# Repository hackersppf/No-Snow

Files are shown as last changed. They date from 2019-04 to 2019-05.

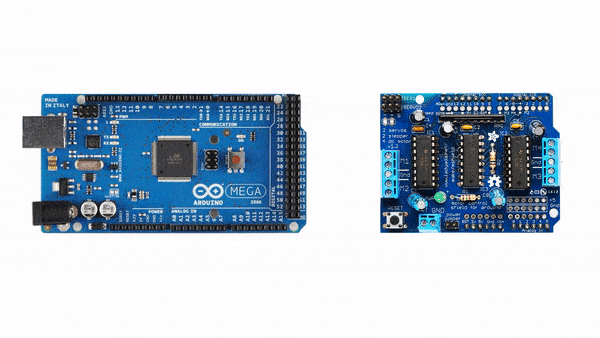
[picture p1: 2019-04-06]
Schematics/Motor Driver Shield connect to Mega.gif

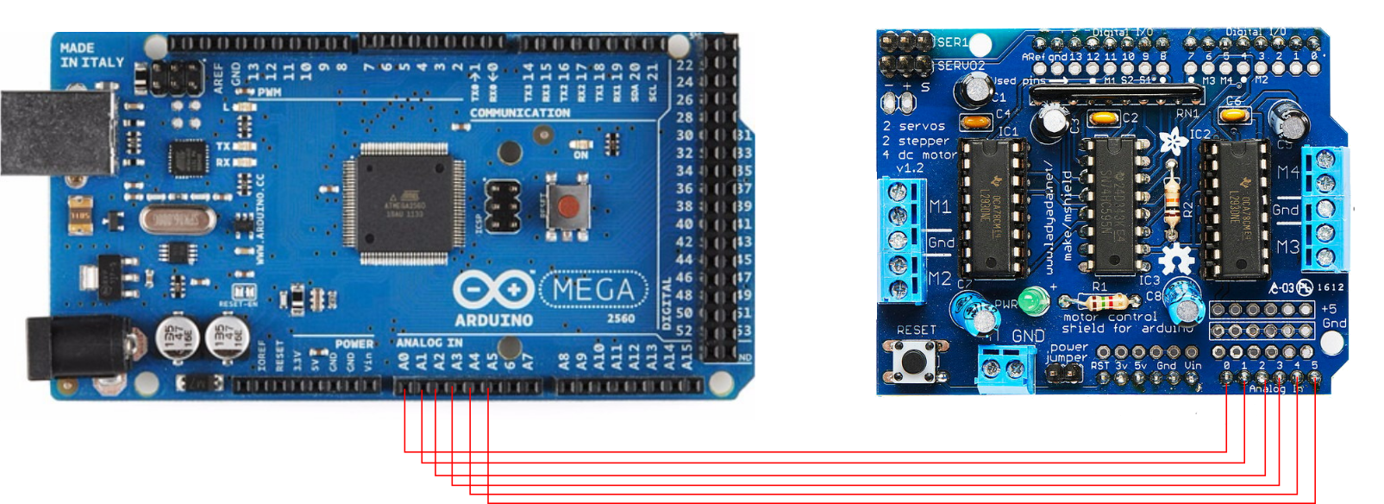
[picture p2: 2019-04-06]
Schematics/Motor Driver Shield connect to Mega.png

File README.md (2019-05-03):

# No-Snow
Ένα αυτόνομο αποχιονιστικό όχημα για τον καθαρισμό των αυλών στα σχολεία της Φλώρινας.
![](https://lh3.googleusercontent.com/xO7sTSYgVaHP3CewTKH7Cif9RfCc6hG_EpvHSLslNRIoFkOp1THHu7uWFASRAP4SzOY6zCx56El4OVzGu1Sz-iZWRYOYOWNuBQ8KCTcxCPi_N1hTWm2V-zk4BNUXDjUctix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)
Στην πόλη μας (Φλώρινα) κατά τους χειμερινούς μήνες έχουμε συχνά χιονοπτώσεις οι οποίες συνοδεύονται από χαμηλές θερμοκρασίες, με αποτέλεσμα προβλήματα στις μετακινήσεις, καθώς και στην λειτουργία των σχολείων. Ύστερα από κάθε ισχυρή χιονόπτωση, τα εκχιονιστικά μηχανήματα του Δήμου δουλεύουν συνεχώς για να καθαρίσουν τους δρόμους της πόλης και των γύρω χωριών, καθώς και τις αυλές των σχολείων πριν προλάβει να παγώσει το χιόνι. Αρκετές φορές τα σχολεία παραμένουν κλειστά γιατί δεν έχουν προλάβει να καθαριστεί οι αυλές, καθώς δίνεται προτεραιότητα τους δρόμους.

Επιλέξαμε λοιπόν να κατασκευάσουμε ένα αυτόνομο αποχιονιστικό μηχάνημα, το οποίο θα αναλαμβάνει να καθαρίσει το χιόνι από έναν συγκεκριμένο χώρο (για παράδειγμα την αυλή ενός σχολείου) χωρίς να χρειάζεται οδηγό.

#### Οι βασικές λειτουργίες που έχει το σύστημα μας είναι οι εξής:
- Μπορεί να κινηθεί σε ευθεία διαδρομή καθαρίζονας το χιόνι με το μαχαίρι και αντιλαμβάνεται τυχόν αποκλίσεις τις οποίες διορθώνει, με την βοήθεια γυροσκόπιου.
- Αντιλαμβάνεται πότε φτάνει στα όρια της αυλής με τον αισθητήρα απόστασης υπέρηχων και μπορεί να συνεχίσει την πορεία του προς την αντίθετη πλευρά με ακρίβεια αξιοποιώντας το γυροσκόπιο.
- Αντιλαμβάνεται την κίνηση ανθρώπων στον χώρο της αυλής (αισθητήρας PIR) και σταματάει εκπέμποντας προειδοποιητικά μηνύματα και φώτα.
- Αντιλαμβάνεται αν υπάρχουν συνθήκες δημιουργίας πάγου (αισθητήρας θερμοκρασίας και βροχόπτωσης) και να ρίχνει αλάτι στην αυλή.
#### Μελλοντικά σχέδια
- Υπολογισμός της θέσης του μέσα στην αυλή του σχολείου αξιοποιώντας τα δεδομένα από το γυροσκόπιο και τον αισθητήρα απόστασης.
- Επικοινωνία με έξυπνα κινητά τηλέφωνα ώστε να στέλνει και να δέχεται δεδομένα για την κατάσταση αποχιονισμού.

**Μπορείτε να διαβάσετε αναλυτικά για την υλοποίηση του έργου [στην ιστοσελίδα του ομίλου μας.](http://ppf.edu.gr/hackers/archives/604 "στην ιστοσελίδα του ομίλου μας.")**

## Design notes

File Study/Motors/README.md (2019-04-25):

Σε αυτό το εργαστήριο μελετήσαμε την αρχή λειτουργίας των κινητήρων DC, Servo και Stepper και τους τρόπους με τους οποίους μπορούμε να τους ελέγξουμε με την χρήση του Arduino. Στο πλαίσιο του εργαστηρίου κατασκευάσαμε και μερικούς ανεμιστήρες με φίλτρο, αξιοποιώντας παλιές συσκευές που υπάρχουν στο υπόγειο του σχολείου, τους οποίους χρησιμοποιήσαμε αργότερα για την απομάκρυνση των οσμών από την κόλληση καλωδίων. Μπορείτε να δείτε περισσότερες λεπτομέρειες στην ανάρτηση που υπάρχει εδώ: http://ppf.edu.gr/hackers/archives/604

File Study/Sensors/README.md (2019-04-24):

Εργαστήριο στο οποίο μελετάμε τον τρόπο με τον οποίο μπορούμε να λαμβάνουμε τιμές από τον φυσικό κόσμο και να τις μετατρέπουμε σε ψηφιακές τιμές με την χρήση αισθητήρων και του Arduino. Περισσότερες λεπτομέρειες στο http://ppf.edu.gr/hackers/archives/55

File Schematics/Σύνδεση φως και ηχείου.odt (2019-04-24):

## Σύνδεση μονάδων φωτός και ήχου

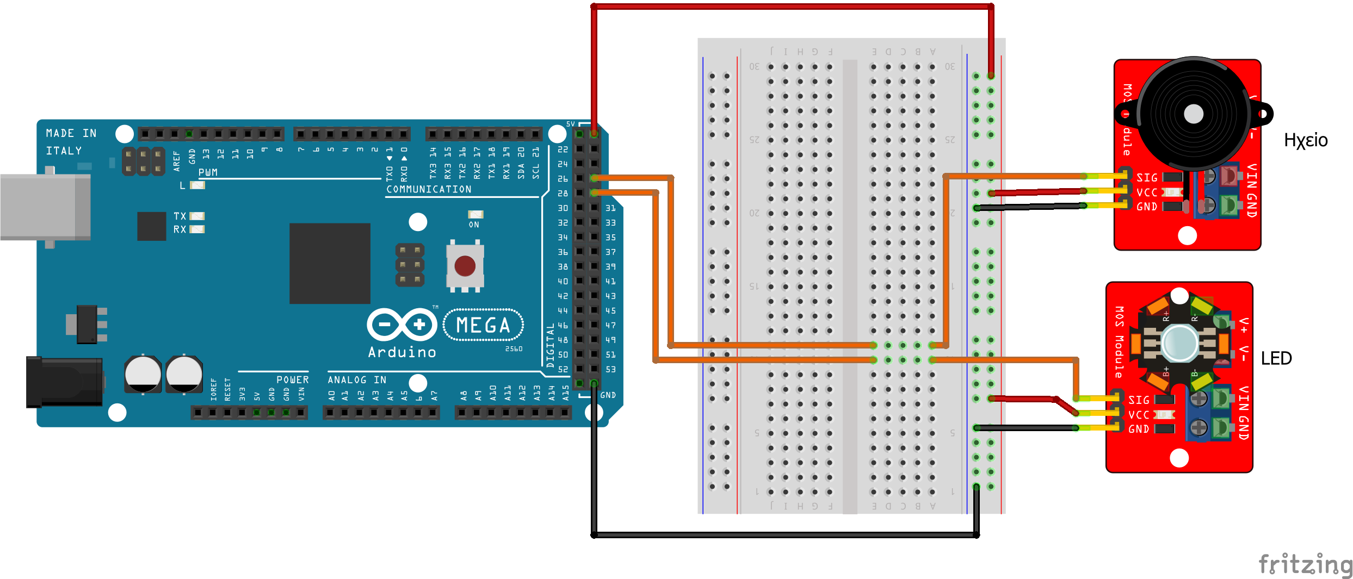
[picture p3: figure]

Μονάδα φωτός | Arduino | Επιθυμητό χρώμα καλωδίου
+ | 5V | Κόκκινο
G | GND | Μαύρο ή καφέ
S | Digital 29 | Πορτοκαλί

Μονάδα ήχου | Arduino | Επιθυμητό χρώμα καλωδίου
+ | 5V | Κόκκινο
- | GND | Μαύρο ή καφέ
S | Digital 27 | Πορτοκαλί

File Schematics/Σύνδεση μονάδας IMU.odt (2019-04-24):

## Σύνδεση μονάδας IMU (Γυροσκόπιο και επιταχυνσιόμετρο)

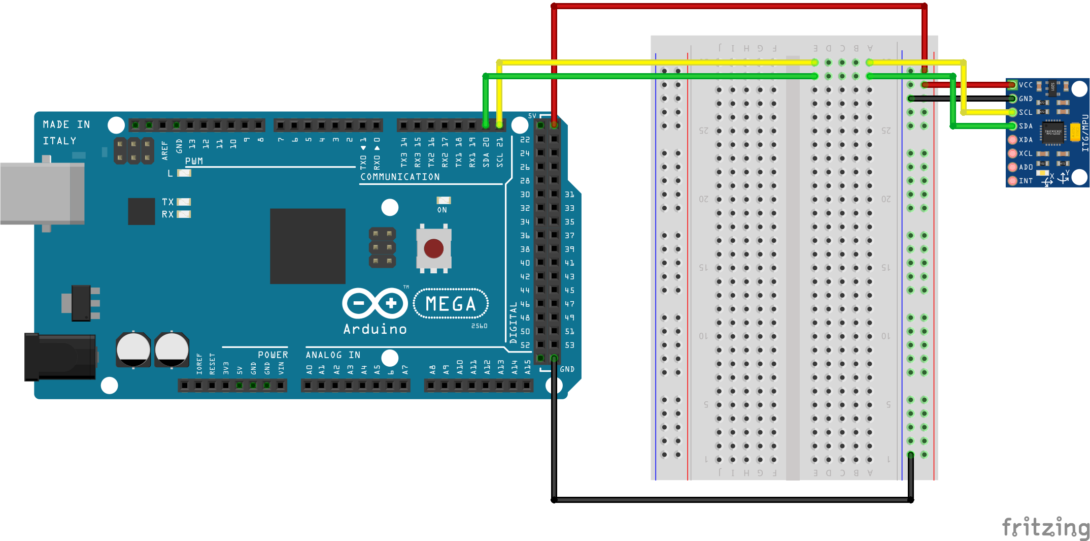
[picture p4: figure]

Μονάδα IMU | Arduino | Επιθυμητό χρώμα καλωδίου
VCC | 5V | Κόκκινο
GND | GND | Μαύρο ή καφέ
SDA | SDA | Πράσινο
SCL | SCL | Κίτρινο

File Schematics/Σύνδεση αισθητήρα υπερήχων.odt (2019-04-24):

## Σύνδεση αισθητήρα υπερήχων - απόστασης

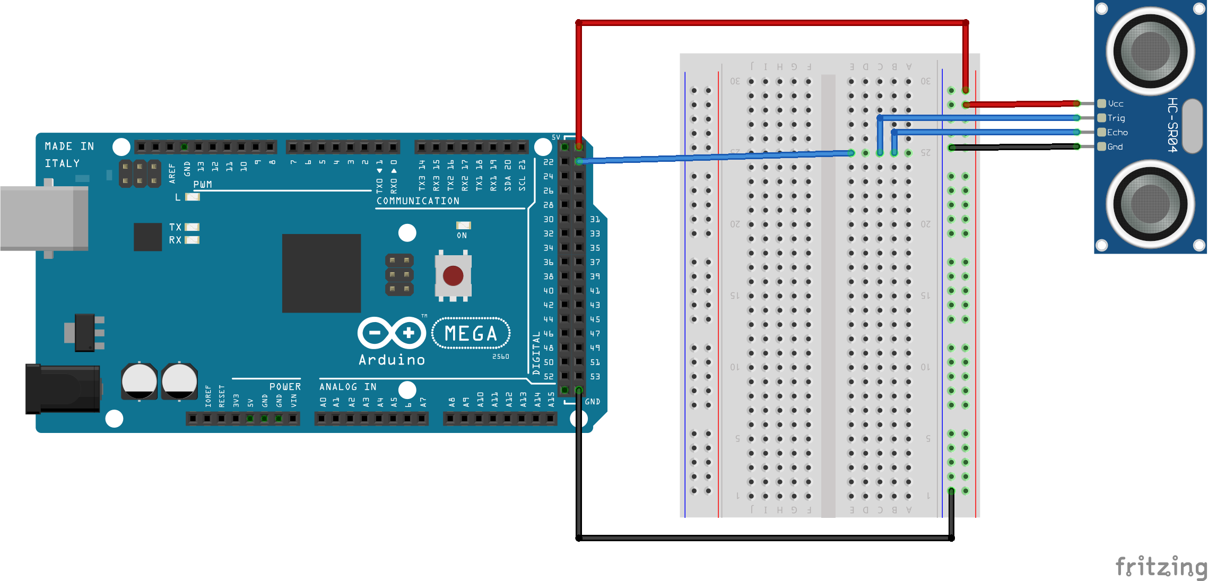
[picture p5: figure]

Αισθητήρας υπερήχων | Arduino | Επιθυμητό χρώμα καλωδίου
VCC | 5V | Κόκκινο
GND | GND | Μαύρο ή καφέ
TRIG | Digital 23 | Μπλε
ECHO | Digital 23 | Μπλε

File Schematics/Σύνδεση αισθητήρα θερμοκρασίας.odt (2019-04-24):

## Σύνδεση αισθητήρα θερμοκρασίας

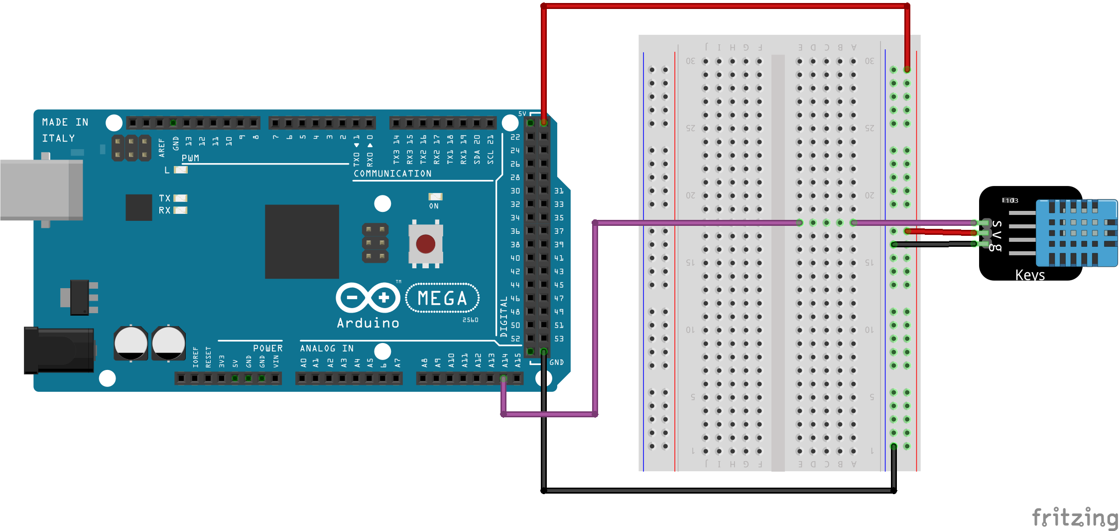
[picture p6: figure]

Αισθητήρας θερμοκρασίας | Arduino | Επιθυμητό χρώμα καλωδίου
VCC ή V ή + | 5V | Κόκκινο ή άσπρο
GND ή – ή G | GND | Μαύρο ή καφέ
SIGNAL ή S ή A0 | Α14 | Μοβ

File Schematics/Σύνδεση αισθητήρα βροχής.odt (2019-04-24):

## Σύνδεση αισθητήρα βροχής

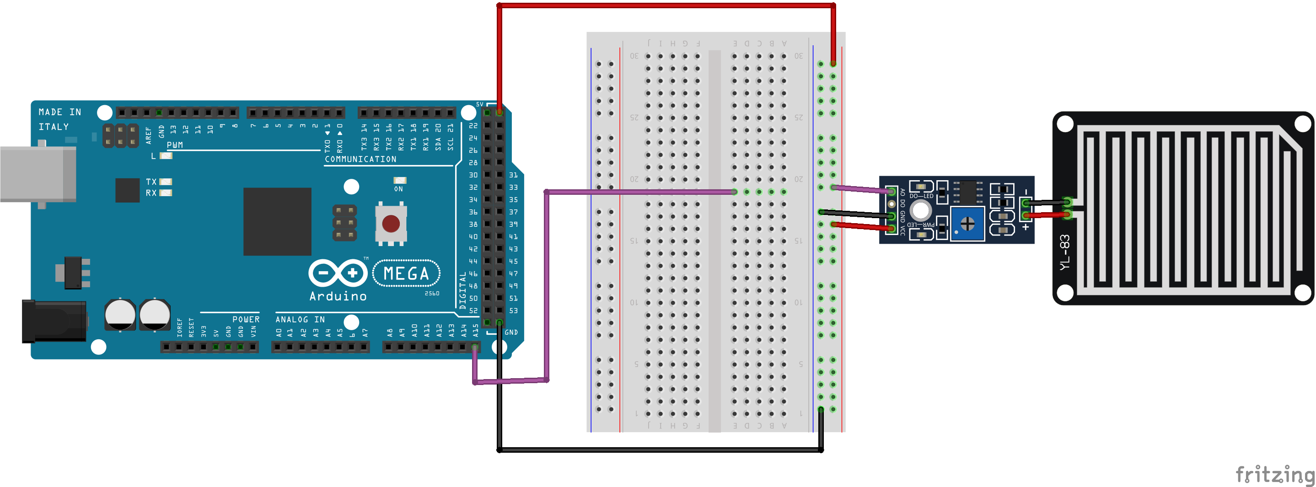
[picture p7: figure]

Αισθητήρας βροχής | Arduino | Επιθυμητό χρώμα καλωδίου
VCC | 5V | Κόκκινο
GND | GND | Μαύρο ή καφέ
Α0 | Α15 | Μοβ

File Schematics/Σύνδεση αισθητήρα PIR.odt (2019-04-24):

## Σύνδεση αισθητήρα κίνησης PIR

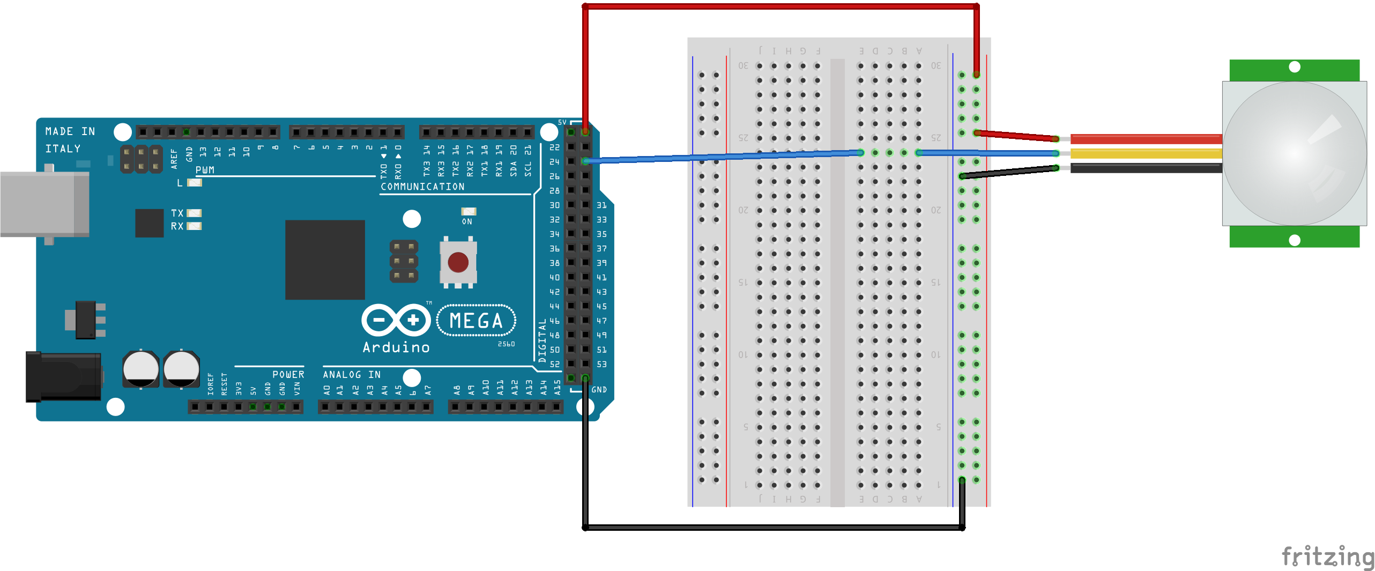
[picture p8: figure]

Μονάδα PIR | Arduino | Επιθυμητό χρώμα καλωδίου
VCC ή + | 5V | Κόκκινο ή άσπρο
GND ή - | GND | Μαύρο ή καφέ
SIGNAL ή OUT | Digital 25 | Μπλε

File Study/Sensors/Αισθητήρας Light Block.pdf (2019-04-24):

## Μαθαίνουμε τους αισθητήρες

## Αισθητήρας μπλοκαρίσματος φωτός

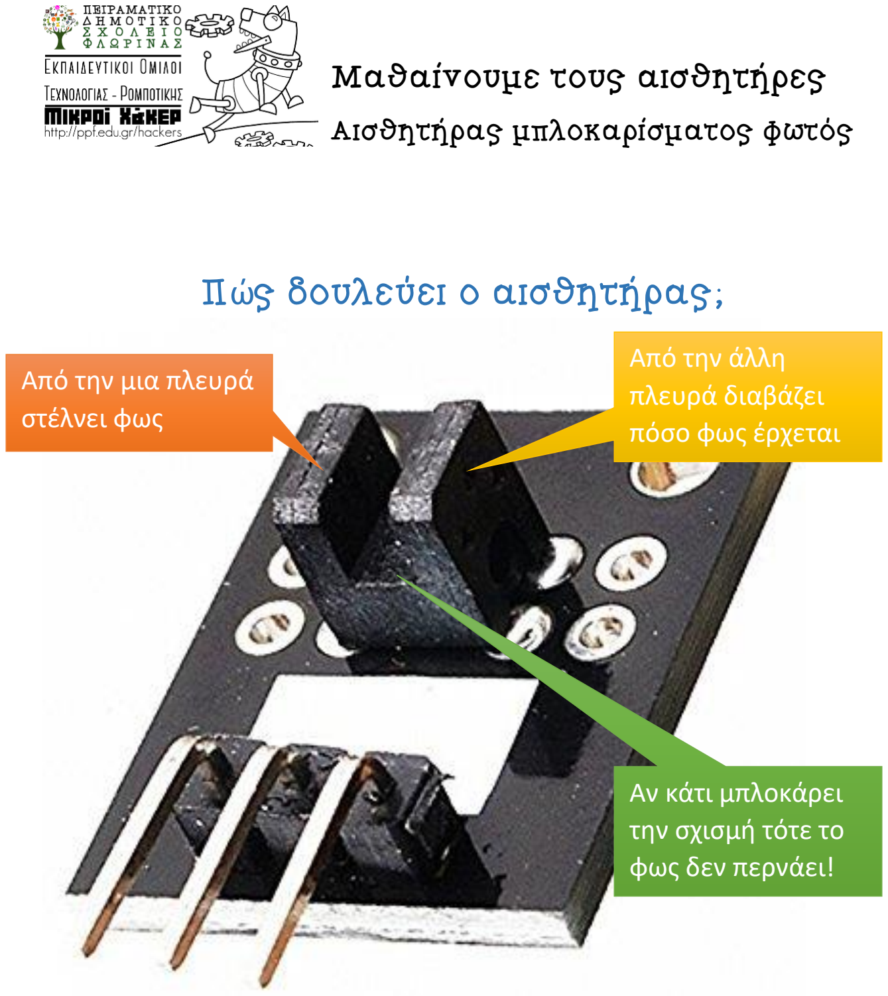
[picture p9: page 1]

Πώς δουλεύει ο αισθητήρας;

## Από την μια πλευρά στέλνει φως

## Από την άλλη πλευρά διαβάζει πόσο φως έρχεται

## Αν κάτι μπλοκάρει την σχισμή τότε το φως δεν περνάει!

# Πώς τον συνδέω στο Arduino

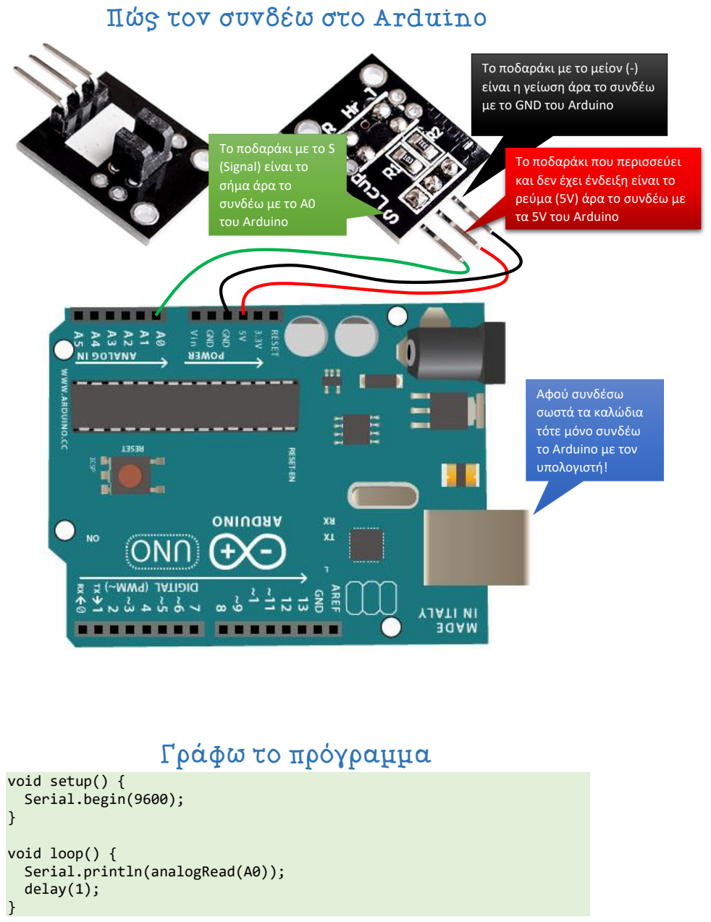
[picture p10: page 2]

# Γράφω το πρόγραμμα

void setup() {
Serial.begin(9600);
}

void loop() {
Serial.println(analogRead(A0)); delay(1);
}

Το ποδαράκι με το μείον (-) είναι η γείωση άρα το συνδέω με το GND του Arduino

Το ποδαράκι με το S
(Signal) είναι το
σήμα άρα το
συνδέω με το A0
του Arduino

Το ποδαράκι που περισσεύει και δεν έχει ένδειξη είναι το ρεύμα (5V) άρα το συνδέω με τα 5V του Arduino

Αφού συνδέσω
σωστά τα καλώδια
τότε μόνο συνδέω
το Arduino με τον
υπολογιστή!

# Ανεβάζω το πρόγραμμα στο Arduino

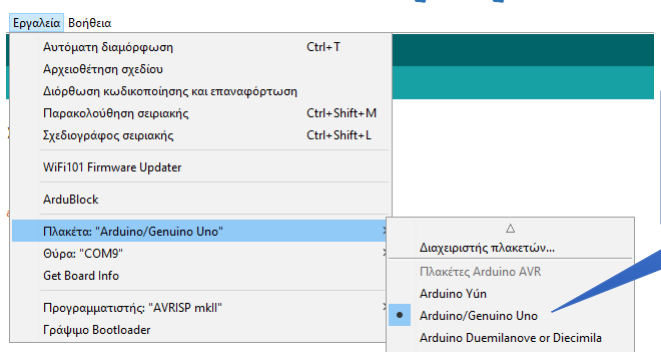
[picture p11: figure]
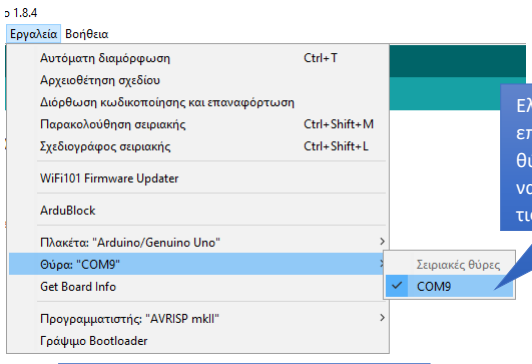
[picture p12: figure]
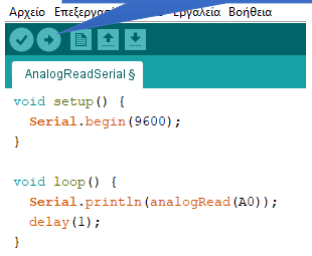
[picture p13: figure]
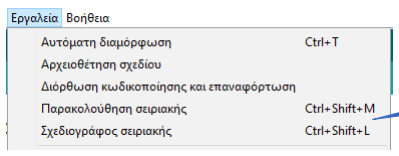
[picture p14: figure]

# Κάνω τα πειράματα μου

## Παρακολουθήστε τις τιμές που έρχονται στο Σειριακό

παράθυρο και απαντήστε στις ερωτήσεις που υπάρχουν εδώ (https://goo.gl/forms/BbE0vTYZVCx2bCOv1)

Ελέγχω ότι έχω
επιλεγμένη την
πλακέτα Arduino Uno

Ελέγχω ότι έχω
επιλεγμένη την τελευταία
θύρα στην λίστα. Μπορεί
να είναι οποιαδήποτε από
τις COM1 μέχρι COM9

Στέλνω το πρόγραμμα μου στο Arduino

Ανοίγω είτε την Παρακολούθηση Σειριακής είτε τον Σχεδιογράφο Σειριακής για να δω τι τιμές στέλνει ο αισθητήρας στο Arduino και αυτό με την σειρά του στον υπολογιστή

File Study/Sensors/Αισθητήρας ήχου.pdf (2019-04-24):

## Μαθαίνουμε τους αισθητήρες

## Αισθητήρας Ήχου

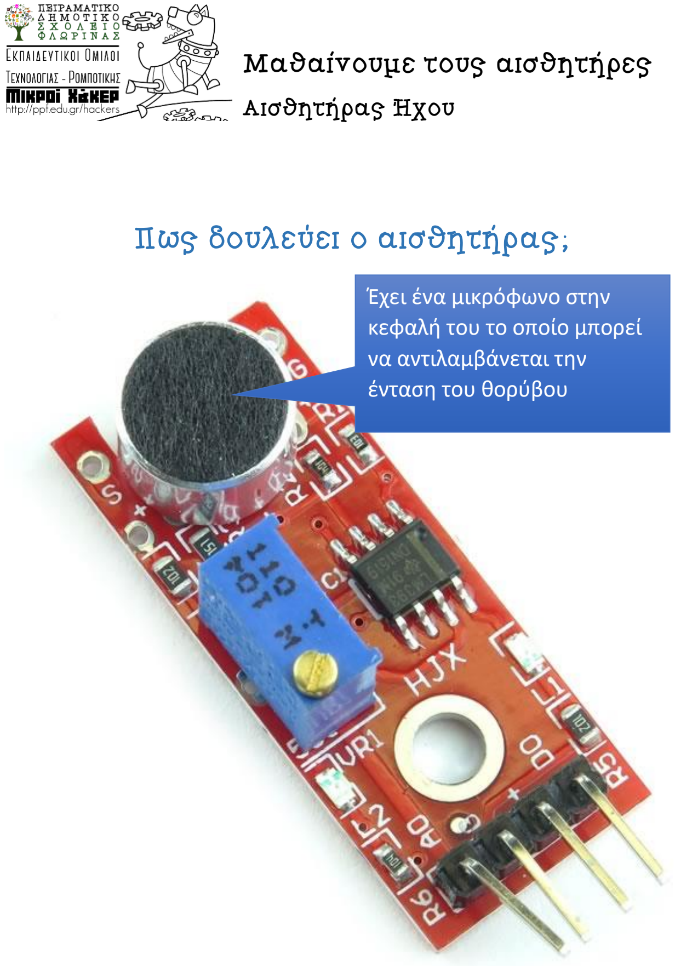
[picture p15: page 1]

Πως δουλεύει ο αισθητήρας;

## Έχει ένα μικρόφωνο στην κεφαλή του το οποίο μπορεί να αντιλαμβάνεται την ένταση του θορύβου

# Πως τον συνδέω στο Arduino

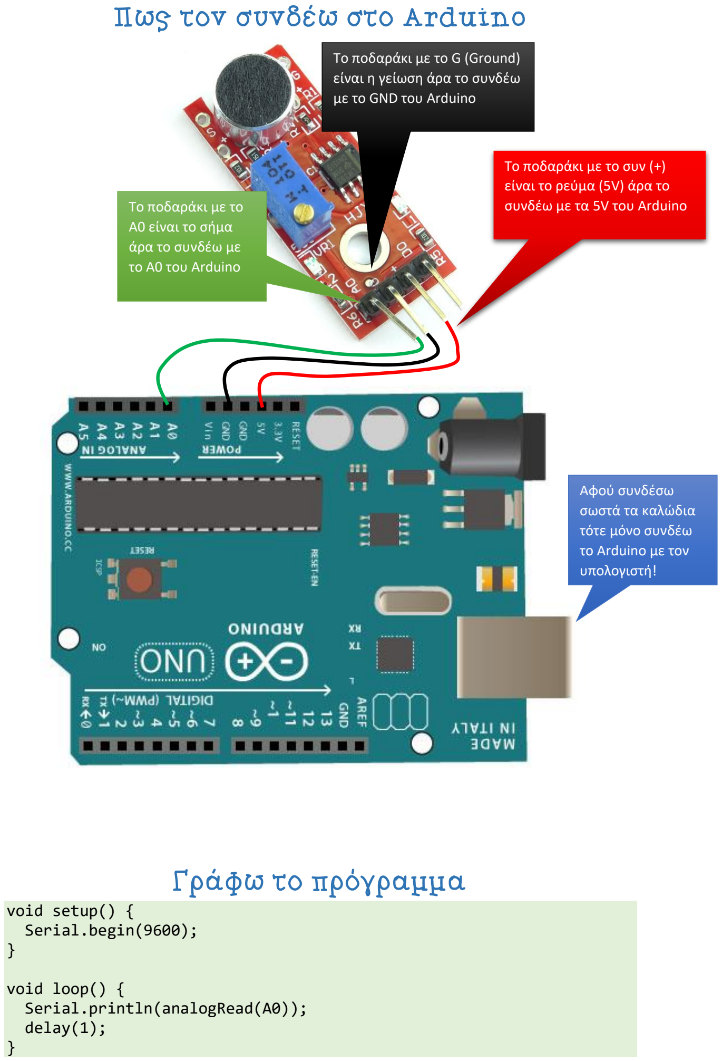
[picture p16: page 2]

# Γράφω το πρόγραμμα

void setup() {
Serial.begin(9600);
}

void loop() {
Serial.println(analogRead(A0)); delay(1);
}

Το ποδαράκι με το G (Ground) είναι η γείωση άρα το συνδέω με το GND του Arduino

Το ποδαράκι με το
Α0 είναι το σήμα
άρα το συνδέω με
το A0 του Arduino

Το ποδαράκι με το συν (+)
είναι το ρεύμα (5V) άρα το συνδέω με τα 5V του Arduino

Αφού συνδέσω
σωστά τα καλώδια
τότε μόνο συνδέω
το Arduino με τον
υπολογιστή!

# Ανεβάζω το πρόγραμμα στο Arduino


# Κάνω τα πειράματα μου

## Παρακολουθήστε τις τιμές που έρχονται στο Σειριακό

παράθυρο και απαντήστε στις ερωτήσεις που υπάρχουν εδώ (https://goo.gl/forms/BbE0vTYZVCx2bCOv1)

Ελέγχω ότι έχω
επιλεγμένη την
πλακέτα Arduino Uno

Ελέγχω ότι έχω
επιλεγμένη την τελευταία
θύρα στην λίστα. Μπορεί
να είναι οποιαδήποτε από
τις COM1 μέχρι COM9

Στέλνω το πρόγραμμα μου στο Arduino

Ανοίγω είτε την Παρακολούθηση Σειριακής είτε τον Σχεδιογράφο Σειριακής για να δω τι τιμές στέλνει ο αισθητήρας στο Arduino και αυτό με την σειρά του στον υπολογιστή

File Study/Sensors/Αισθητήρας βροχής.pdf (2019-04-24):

## Μαθαίνουμε τους αισθητήρες

## Αισθητήρας Στάθμης νερού

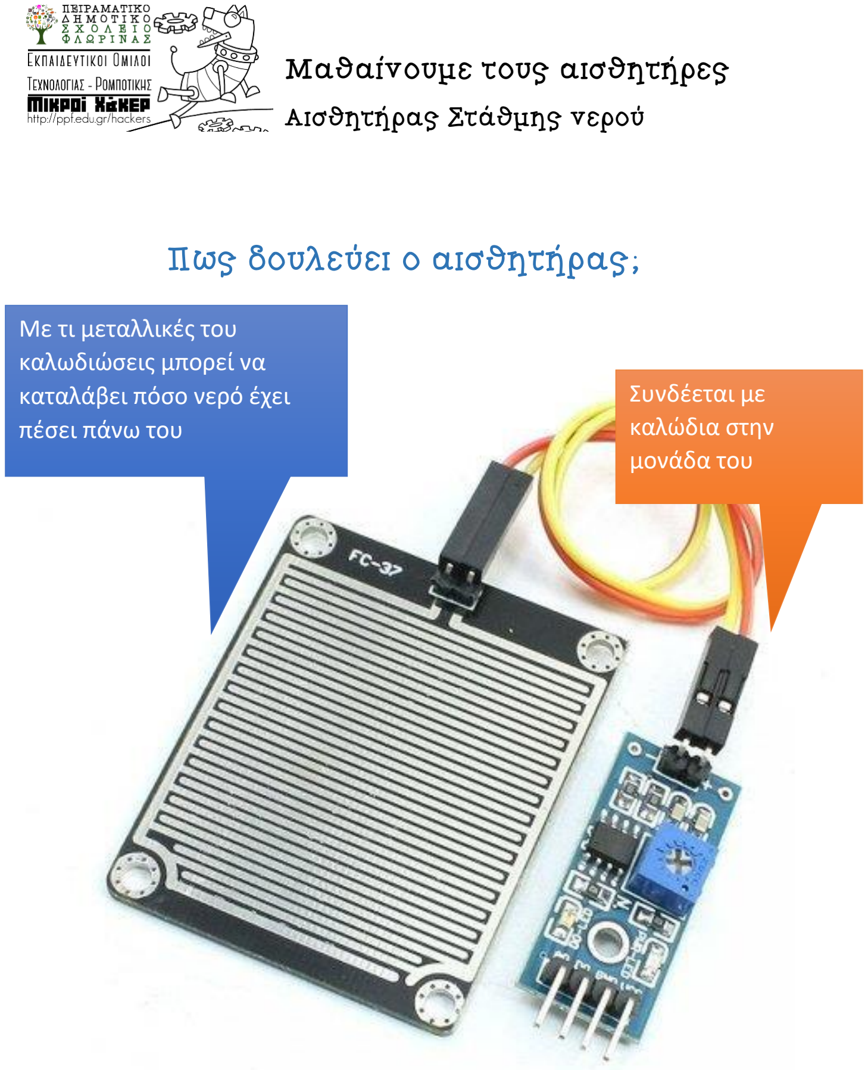
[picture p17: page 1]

Πως δουλεύει ο αισθητήρας;

## Με τι μεταλλικές του καλωδιώσεις μπορεί να καταλάβει πόσο νερό έχει πέσει πάνω του

## Συνδέεται με καλώδια στην μονάδα του

# Πως τον συνδέω στο Arduino

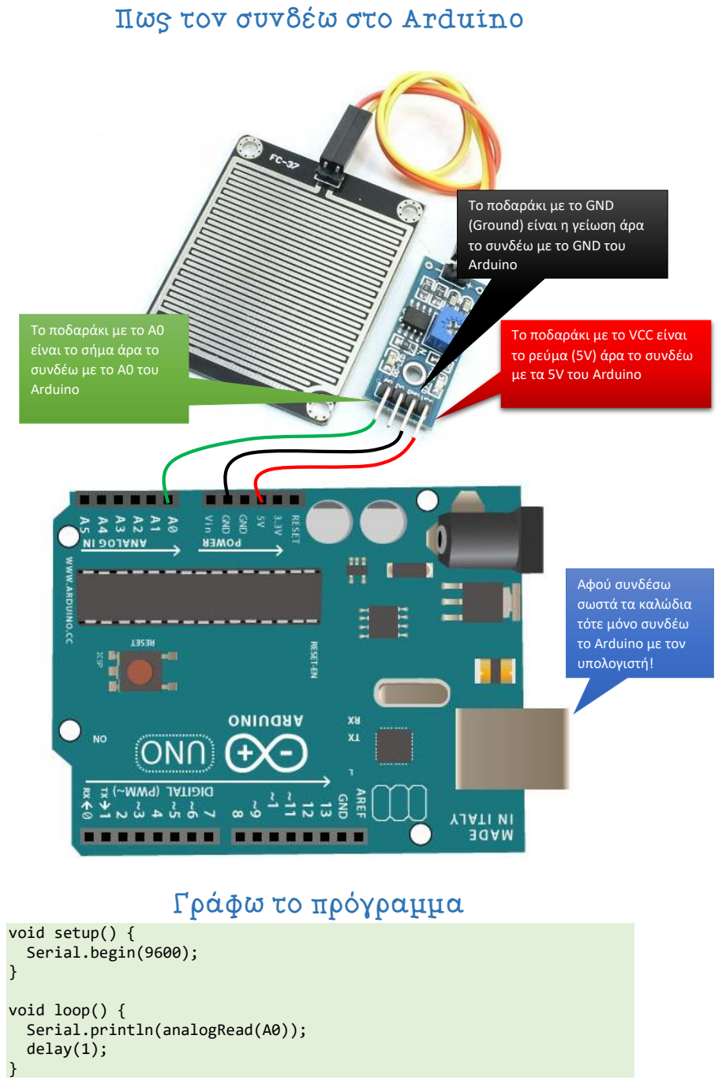
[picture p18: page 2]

# Γράφω το πρόγραμμα

void setup() {
Serial.begin(9600);
}

void loop() {
Serial.println(analogRead(A0)); delay(1);
}

Το ποδαράκι με το GND
(Ground) είναι η γείωση άρα το συνδέω με το GND του
Arduino

Το ποδαράκι με το A0
είναι το σήμα άρα το
συνδέω με το A0 του
Arduino

Το ποδαράκι με το VCC είναι το ρεύμα (5V) άρα το συνδέω με τα 5V του Arduino

Αφού συνδέσω
σωστά τα καλώδια
τότε μόνο συνδέω
το Arduino με τον
υπολογιστή!

# Ανεβάζω το πρόγραμμα στο Arduino

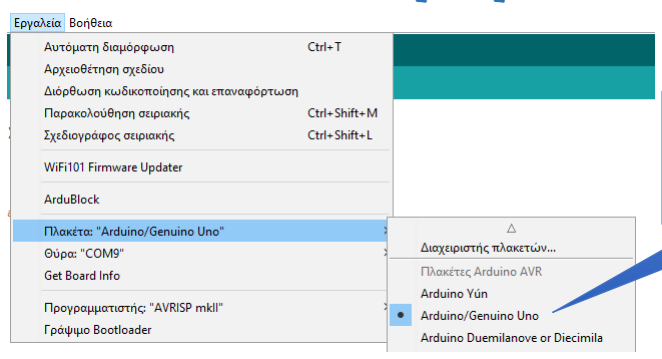
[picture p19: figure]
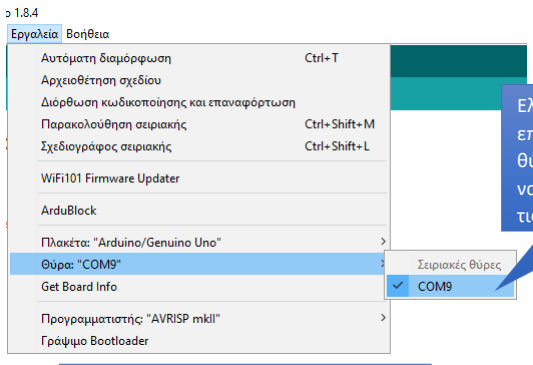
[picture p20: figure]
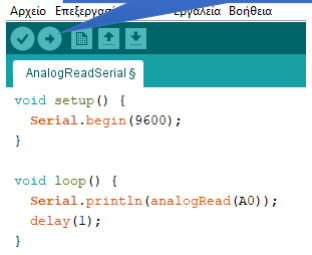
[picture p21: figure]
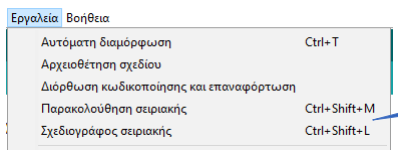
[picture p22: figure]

# Κάνω τα πειράματα μου

## Παρακολουθήστε τις τιμές που έρχονται στο Σειριακό

παράθυρο και απαντήστε στις ερωτήσεις που υπάρχουν εδώ (https://goo.gl/forms/BbE0vTYZVCx2bCOv1)

Ελέγχω ότι έχω
επιλεγμένη την
πλακέτα Arduino Uno

Ελέγχω ότι έχω
επιλεγμένη την τελευταία
θύρα στην λίστα. Μπορεί
να είναι οποιαδήποτε από
τις COM1 μέχρι COM9

Στέλνω το πρόγραμμα μου στο Arduino

Ανοίγω είτε την Παρακολούθηση Σειριακής είτε τον Σχεδιογράφο Σειριακής για να δω τι τιμές στέλνει ο αισθητήρας στο Arduino και αυτό με την σειρά του στον υπολογιστή

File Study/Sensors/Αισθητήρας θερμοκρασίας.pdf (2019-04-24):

## Μαθαίνουμε τους αισθητήρες

## Αισθητήρας θερμοκρασίας

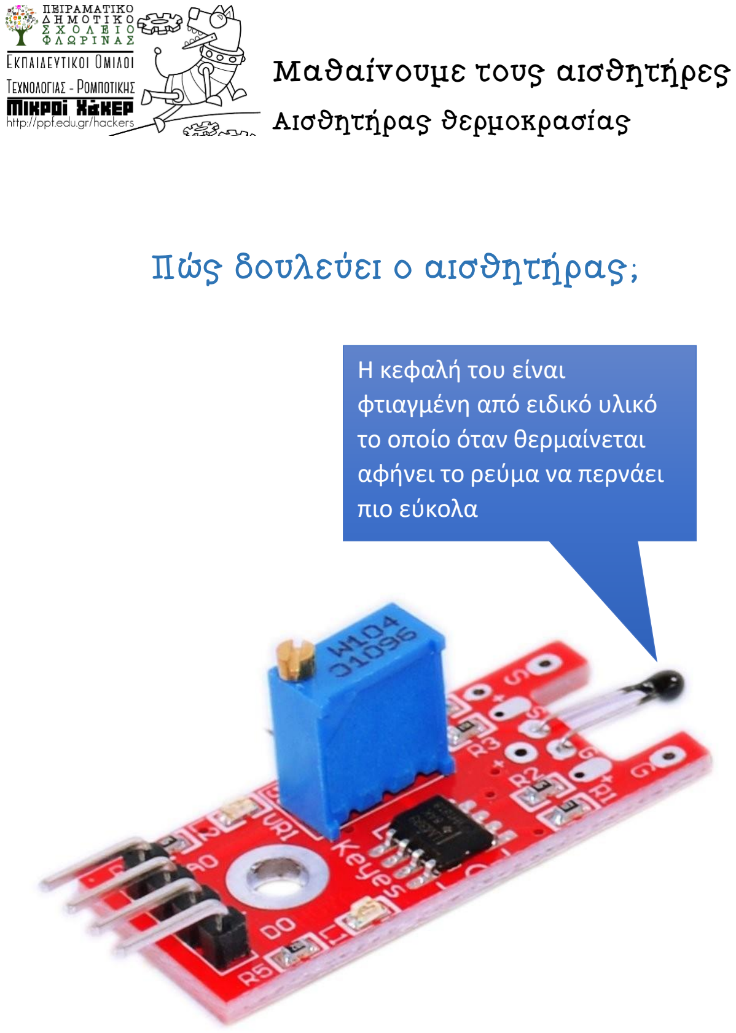
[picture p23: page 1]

Πώς δουλεύει ο αισθητήρας;

## Η κεφαλή του είναι φτιαγμένη από ειδικό υλικό το οποίο όταν θερμαίνεται αφήνει το ρεύμα να περνάει πιο εύκολα

# Πώς τον συνδέω στο Arduino

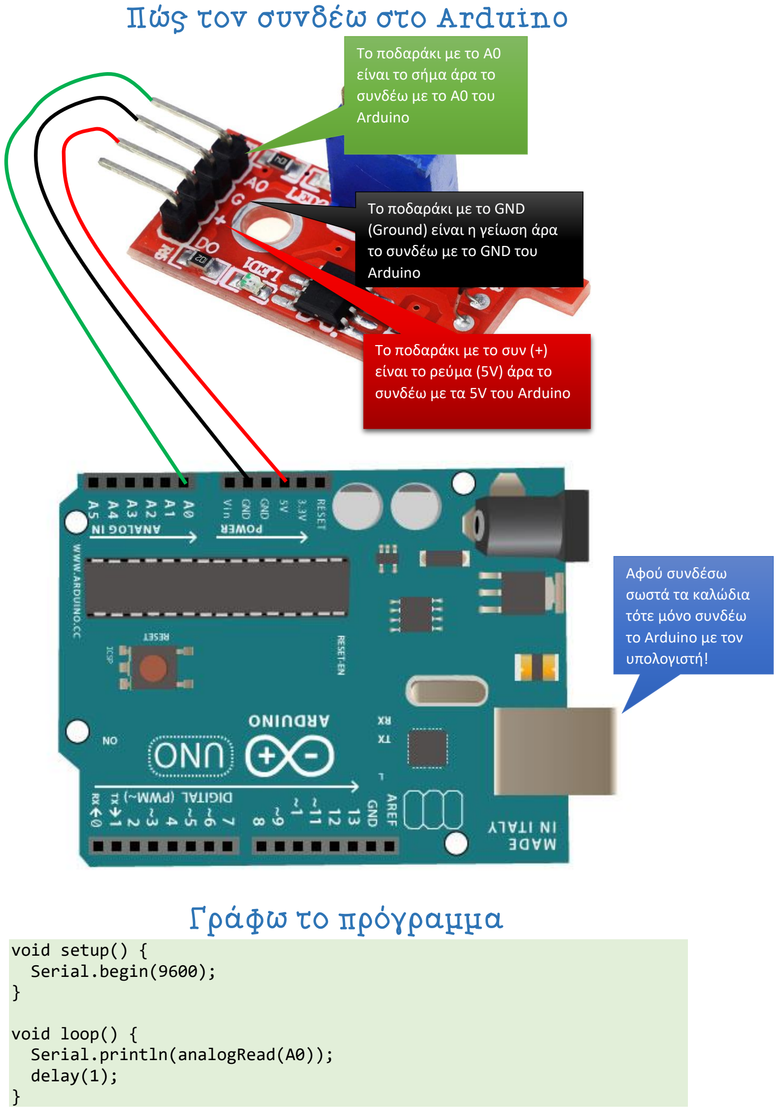
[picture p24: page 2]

# Γράφω το πρόγραμμα

void setup() {
Serial.begin(9600);
}

void loop() {
Serial.println(analogRead(A0)); delay(1);
}

Το ποδαράκι με το GND
(Ground) είναι η γείωση άρα το συνδέω με το GND του
Arduino

Το ποδαράκι με το A0
είναι το σήμα άρα το
συνδέω με το A0 του
Arduino

Το ποδαράκι με το συν (+)
είναι το ρεύμα (5V) άρα το συνδέω με τα 5V του Arduino

Αφού συνδέσω
σωστά τα καλώδια
τότε μόνο συνδέω
το Arduino με τον
υπολογιστή!

# Ανεβάζω το πρόγραμμα στο Arduino


# Κάνω τα πειράματα μου

## Παρακολουθήστε τις τιμές που έρχονται στο Σειριακό

παράθυρο και απαντήστε στις ερωτήσεις που υπάρχουν εδώ (https://goo.gl/forms/BbE0vTYZVCx2bCOv1)

Ελέγχω ότι έχω
επιλεγμένη την
πλακέτα Arduino Uno

Ελέγχω ότι έχω
επιλεγμένη την τελευταία
θύρα στην λίστα. Μπορεί
να είναι οποιαδήποτε από
τις COM1 μέχρι COM9

Στέλνω το πρόγραμμα μου στο Arduino

Ανοίγω είτε την Παρακολούθηση Σειριακής είτε τον Σχεδιογράφο Σειριακής για να δω τι τιμές στέλνει ο αισθητήρας στο Arduino και αυτό με την σειρά του στον υπολογιστή

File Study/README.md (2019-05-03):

Εργαστηριακά μαθήματα που πραγματοποιήσαμε κατά την διάρκεια της υλοποίησης του έργου για την μελέτη των μηχανισμών και των μονάδων που χρησιμοποιούμε.

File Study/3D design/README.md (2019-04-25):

Η ΕΛΛΑΚ έχει παραχωρήσει στον όμιλο μας έναν τρισδιάστατο εκτυπωτή RepRap Prusa, τον οποίο αξιοποιούμε κάθε χρόνο στις κατασκευές μας. Για την εισαγωγή των μαθητών στις έννοιες της 3Δ σχεδίασης και εκτύπωσης αφιερώσαμε μια συνάντηση στην πλατφόρμα tinkercad. Μπορείτε να δείτε παραπάνω λεπτομέρειες σε αυτή την ανάρτηση:http://ppf.edu.gr/hackers/archives/506

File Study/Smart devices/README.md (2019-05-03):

Εργαστήριο με σκοπό την συζήτηση του όρου "έξυπνες συσκευές" http://ppf.edu.gr/hackers/archives/881

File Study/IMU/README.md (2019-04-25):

Ο τρόπος με τον οποίο τα αυτόνομα αποχιονιστικά μας θα κρατάν σταθερή την πορεία τους στον χώρο, βασίζεται στην μονάδα πλοήγησης αδράνειας (IMU) που διαθέτουν. Μια τέτοια μονάδα περιλαμβάνει δυο βασικούς αισθητήρες: επιταχυνσιομέτρο και γυροσκόπιο. Για την μελέτη αυτών των αισθητήρων αφιερώσαμε μια συνάντηση του ομίλου μας. Μπορείτε να δείτε αναλυτικά το εργαστήριο σε αυτή την ανάρτηση: http://ppf.edu.gr/hackers/archives/785

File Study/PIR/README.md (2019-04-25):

Ένας από τους αισθητήρες που θα περιλαμβάνουν τα αυτόνομα αποχιονιστικά μας, είναι ο αισθητήρας κίνησης PIR για την ανίχνευση κινήσεων από ανθρώπους. Με τον τρόπο αυτό θα προσπαθήσουμε να αποφύγουμε τυχόν ατυχήματα που θα μπορούσαν να σημειωθούν. Στο εργαστήριο που πραγματοποιήσαμε, μελετήσαμε την αρχή λειτουργίας των αισθητήρων PIR, ενώ τα παιδιά κατασκεύασαν και προγραμμάτισαν ένα απλό κύκλωμα ειδοποίησης, συμπεριλαμβάνοντας λαμπάκια led και μονάδες buzzer. Αναλυτικά το εργαστήριο μπορείτε να το δείτε σε αυτή την ανάρτηση: http://ppf.edu.gr/hackers/archives/565

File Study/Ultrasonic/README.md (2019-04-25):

Στα αυτόνομα αποχιονιστικά που σχεδιάζουμε χρησιμοποιούμε αισθητήρες απόστασης υπερήχων για να υπολογίζουμε την απόσταση των οχημάτων από εμπόδια. Για την μελέτη αυτών των αισθητήρων αφιερώσαμε μια συνάντηση του ομίλου μας. Μπορείτε να δείτε αναλυτικά το εργαστήριο σε αυτή την ανάρτηση: http://ppf.edu.gr/hackers/archives/539

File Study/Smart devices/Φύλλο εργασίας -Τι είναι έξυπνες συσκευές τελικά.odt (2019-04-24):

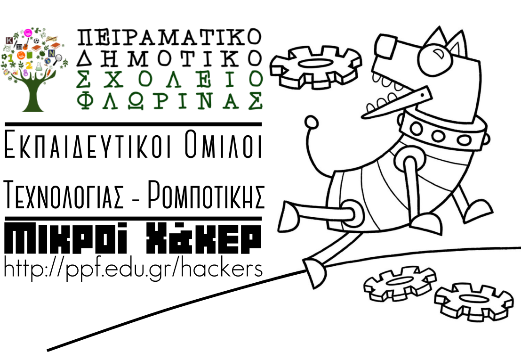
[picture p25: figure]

Τι είναι έξυπνες συσκευές τελικά;

Ονοματεπώνυμο: …………………………………………

Ποια παιδιά είναι στην ομάδα μου;

………………………………………………………………………

………………………………………………………………………

………………………………………………………………………

Μια έξυπνη συσκευή μπορεί να αισθάνεται πράγματα που συμβαίνουν γύρω της, να σκέφτεται σύμφωνα με κάποιες οδηγίες και να ενεργεί κάνοντας κάποια δουλειά μόνη της.

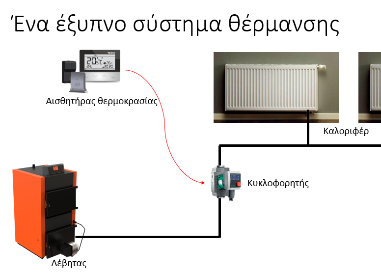
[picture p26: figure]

Ένα έξυπνο σύστημα θέρμανσης:

Αισθάνεται: Θερμοκρασία σπιτιού

Σκέφτεται: Ελέγχει αν είναι μικρότερη ή μεγαλύτερη από αυτή που θέλουν οι κάτοικοι του σπιτιού.

Ενεργεί: Στέλνει ζεστό νερό στα καλοριφέρ.

Δραστηριότητα 1: Στην σελίδα του ομίλου ppf.edu.gr/hackers υπάρχουν οι κατασκευές που είχαν κάνει τα παιδιά που συμμετείχαν τις δυο προηγούμενες χρονιές. Επιλέξτε τον Αυτόματα περιστρεφόμενο ηλιακό συλλέκτη και παρακολουθήστε το βίντεο που έχει.

Τι αισθάνεται:…………………………………………………………………………………………………………………………

……………………………………………………………………………………………………………………………………………….

Πώς σκέφτεται:……………………………………………………………………………………………………………………….

……………………………………………………………………………………………………………………………………………….

Πώς ενεργεί:……………………………………………………………………………………………………………………………

……………………………………………………………………………………………………………………………………………….

Δραστηριότητα 2: Στην σελίδα του ομίλου ppf.edu.gr/hackers υπάρχουν οι κατασκευές που είχαν κάνει τα παιδιά που συμμετείχαν τις δυο προηγούμενες χρονιές. Επιλέξτε τον Έξυπνο κάδος με το arduino και παρακολουθήστε το βίντεο που έχει.

Τι αισθάνεται:…………………………………………………………………………………………………………………………

……………………………………………………………………………………………………………………………………………….

Πώς σκέφτεται: :…………………………………………………………………………………………………………………….

……………………………………………………………………………………………………………………………………………….

Πώς ενεργεί: :…………………………………………………………………………………………………………………………

……………………………………………………………………………………………………………………………………………….

Δραστηριότητα 3: Ποια από τις κατασκευές που υπάρχουν στην σελίδα του ομίλου ppf.edu.gr/hackers σας άρεσε περισσότερο; Γιατί;

……………………………………………………………………………………………………………………………………………….

……………………………………………………………………………………………………………………………………………….

……………………………………………………………………………………………………………………………………………….

……………………………………………………………………………………………………………………………………………….

……………………………………………………………………………………………………………………………………………….

……………………………………………………………………………………………………………………………………………….

……………………………………………………………………………………………………………………………………………….

……………………………………………………………………………………………………………………………………………….

Δραστηριότητα 4: Στην σελίδα του ομίλου ppf.edu.gr/hackers υπάρχουν οι κατασκευές που είχαν κάνει τα παιδιά που συμμετείχαν τις δυο προηγούμενες χρονιές. Επιλέξτε την Έξυπνη λάμπα με το arduino. Η λάμπα αυτή είναι αυτόματη και ανάβει μόνη της όταν πέσει το σκοτάδι. Έχει έναν αισθητήρα που καταλαβαίνει πόσο φως υπάρχει στο δωμάτιο και σκέφτεται ως εξής: Αν το φως είναι ικανοποιητικό τότε σβήνει την λάμπα, αλλιώς ανάβει την λάμπα. Την έχω τοποθετήσει στο γραφείο μου και το πρόβλημα που αντιμετωπίζω είναι το εξής: Η λάμπα συνεχίζει να ανάβει τα βράδια ακόμα και όταν εγώ λείπω από το γραφείο και ξοδεύει τις μπαταρίες της χωρίς να χρειάζεται. Πως θα μπορούσαμε να την βελτιώσουμε;

……………………………………………………………………………………………………………………………………………….

……………………………………………………………………………………………………………………………………………….

……………………………………………………………………………………………………………………………………………….

……………………………………………………………………………………………………………………………………………….

……………………………………………………………………………………………………………………………………………….

……………………………………………………………………………………………………………………………………………….

……………………………………………………………………………………………………………………………………………….

……………………………………………………………………………………………………………………………………………….

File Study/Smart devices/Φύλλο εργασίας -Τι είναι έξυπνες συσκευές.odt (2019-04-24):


Τι είναι έξυπνες συσκευές - ρομπότ;

Ονοματεπώνυμο: …………………………………………

Ποια παιδιά είναι στην ομάδα μου;

………………………………………………………………………

………………………………………………………………………

………………………………………………………………………

Αποτέλεσμα εικόνας για smart tv
Αποτέλεσμα εικόνας για telephone
Αποτέλεσμα εικόνας για smartphone

Δραστηριότητα 1: Κύκλωσε με μολύβι όσα από τα παρακάτω αντικείμενα πιστεύεις ότι είναι έξυπνες συσκευές - ρομπότ.

Ασύρματο τηλέφωνο Smartphone

Smart TV

Αποτέλεσμα εικόνας για thermometer
Αποτέλεσμα εικόνας για autopilot

Ψηφιακό θερμόμετρο Αυτόνομο αυτοκίνητο Τηλεκατευθυνόμενο αυτοκινητάκι

Αποτέλεσμα εικόνας για bluetooth speakers
Αποτέλεσμα εικόνας για hand drill
Αποτέλεσμα εικόνας για washing machine

Πλυντήριο ρούχων

Ηχεία Bluetooth Ηλεκτρικό τρυπάνι

Δραστηριότητα 2: Τι είναι λοιπόν έξυπνη συσκευή; Μπορείς να την ορίσεις με μια πρόταση; Ίσως σε βοηθήσουν και κάποιες από τις παρακάτω λέξεις.

Έξυπνη συσκευή είναι .……………………………………………………………………………………………………

……………………………………………………………………………………………………………………………………………

……………………………………………………………………………………………………………………………………………

συσκευές……………………………………………………………………………………………………………………………………………

μηχάνημα δεδομένα πετάει αισθάνεται σκέφτεται υπολογιστής

αποφασίζει οδηγίες αναγνωρίζει ενεργεί ακολουθεί κινείται εξερευνάει

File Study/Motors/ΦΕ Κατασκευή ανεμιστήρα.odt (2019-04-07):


Κατασκευή ανεμιστήρα απομάκρυνσης οσμών κόλλησης.

## Υλικά που θα χρειαστείτε.

- Έναν ανεμιστήρα από παλιό ηλεκτρονικό υπολογιστή (τον παίρνεται από το εργαστήριο),
- Ένα καπελάκι για μπαταρία 9 volt (το παίρνεται από το εργαστήριο),
- Έναν διακόπτη ON-OFF (τον παίρνεται από το εργαστήριο),
- Μια μπαταρία 9 volt,
- Ένα κομμάτι φίλτρου για απορροφητήρα,
- Χαρτόνι ή χαρτόκουτο για την βάση συναρμολόγησης.

## Οδηγίες σύνδεσης

Οι πιο πολλοί ανεμιστήρες από παλιούς υπολογιστές έχουν δυο καλώδια. Το ένα πρέπει να συνδεθεί στο συν (+) της μπαταρίας και το άλλο στο πλην (-). Αν θέλουμε να αλλάξουμε την φορά περιστροφής του ανεμιστήρα τότε πολύ απλά αλλάζουμε την θέση των δυο καλωδίων.


## Προσθήκη φίλτρου

Τοποθετήστε τον ανεμιστήρα πάνω σε ένα κομμάτι φίλτρου απορροφητήρα και σχεδιάστε με ένα μολύβι το περίγραμμα του ανεμιστήρα. Στη συνέχεια κόψτε με ένα ψαλίδι το φίλτρο ώστε να εφαρμόζει ακριβώς στον ανεμιστήρα σας. Με λίγη κόλλα ή σιλικόνη κολλήστε το πάνω στο περίλβημα του ανεμιστήρα.

## Κατασκευή βάσης

Χρησιμοποιήστε την φαντασία σας και ότι υλικά έχετε πρόχειρα στο σπίτι για να κατασκευάσετε την βάση του ανεμιστήρα σας.

Creative Commons Αναφορά Δημιουργού - Παρόμοια Διανομή 4.0 Διεθνές

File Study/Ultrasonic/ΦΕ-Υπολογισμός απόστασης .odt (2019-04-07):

Μικροί Χάκερ -Μέτρηση απόστασης με τον αισθητήρα υπερήχων


Ένας από τους τρόπους για να μετρήσουμε την απόσταση εντός αντικειμένου από την συσκευή μας είναι ο αισθητήρας υπέρηχων. Η λειτουργία του στηρίζεται στο γεγονός πως ξέρουμε την ταχύτητα με την οποία ταξιδεύει ο ήχος (343 μέτρα κάθε δευτερόλεπτο), ενώ επίσης ξέρουμε πως όταν ο ήχος χτυπήσει πάνω στα περισσότερα αντικείμενα γυρνάει προς τα πίσω (ανάκλαση). Μπορείτε να διαβάσετε περισσότερα στο site του ομίλου μας (ppf.edu.gr/hackers/archives/539)

# Πως θα καταλάβουμε την απόσταση από τον αισθητήρα

Για να καταλάβουμε την απόσταση κάποιου αντικειμένου, χρησιμοποιώντας τον αισθητήρα υπέρηχων, θα πρέπει να στείλουμε έναν υπέρηχο και να περιμένουμε να τον λάβει πίσω ο αισθητήρας. Ο αισθητήρας θα μας δώσει τον χρόνο που πέρασε μέχρι να επιστρέψει ο υπέρηχος εκφρασμένο σε μικροδευτερόλεπτα (μsec), δηλαδή εκατομμυριοστά του δευτερολέπτου. Επίσης γνωρίζουμε ότι ο ήχος ταξιδεύει 343 μέτρα κάθε δευτερόλεπτο. Με αυτά τα δεδομένα πως θα βρούμε την απόσταση του αντικειμένου που βρίσκεται μπροστά από την συσκευή;

## Βήμα 1^ο

Ο χρόνος που παίρνουμε από τον αισθητήρα είναι σε μικροδευτερόλεπτα (εκατομμυριοστά του δευτερολέπτου), αλλά εμείς ξέρουμε την ταχύτητα του ήχου εκφρασμένη σε μέτρα ανά δευτερόλεπτο. Θα μετατρέψουμε λοιπόν τον χρόνο σε δευτερόλεπτα.

Άρα ........................................................................................................................................................................................................................................................................................................................

## Βήμα 2^ο

Τώρα που ξέρουμε τον χρόνο που έκανε για να γυρίσει ο υπέρηχος σε δευτερόλεπτα, μπορούμε να βρούμε την απόσταση σε μέτρα. Ξέρουμε ότι ο ήχος σε 1 δευτερόλεπτο ταξιδεύει 343 μέτρα.

Άρα ........................................................................................................................................................................................................................................................................................................................

## Βήμα 3^ο

Τώρα γνωρίζουμε την απόσταση σε μέτρα. Μπορούμε να την μετατρέψουμε σε εκατοστά;


## Βήμα 4^ο

Θα πρέπει τώρα να σκεφτούμε ότι η απόσταση που υπολογίσαμε αφορά το ταξίδι του υπερήχου μέχρι το εμπόδιο καθώς και την επιστροφή του. Εμείς όμως θέλουμε να υπολογίσουμε μόνο την απόσταση μέχρι το εμπόδιο.

Άρα ........................................................................................................................................................................................................................................................................................................................

# Εξάσκηση

1. Αν ο αισθητήρας διαβάσει την τιμή 6000 μικροδευτερόλεπτα σε τι απόσταση βρίσκεται το αντικείμενο μπροστά του;
  1. Βήμα 1 – Μετατροπή σε δευτερόλεπτα: .................................................................
  2. Βήμα 2 – Υπολογισμός μέτρων: ..................................................................
  3. Βήμα 3 – Μετατροπή σε εκατοστά: ........................................................…
  4. Βήμα 4 – Διαίρεση με το 2 : .................................................................
2. Αν ο αισθητήρας διαβάσει την τιμή 1200 μικροδευτερόλεπτα σε τι απόσταση βρίσκεται το αντικείμενο μπροστά του;
  1. Βήμα 1 – Μετατροπή σε δευτερόλεπτα: .................................................................
  2. Βήμα 2 – Υπολογισμός μέτρων: ..................................................................
  3. Βήμα 3 – Μετατροπή σε εκατοστά: ........................................................…
  4. Βήμα 4 – Διαίρεση με το 2 : .................................................................
3. Αν ο αισθητήρας διαβάσει την τιμή 500 μικροδευτερόλεπτα σε τι απόσταση βρίσκεται το αντικείμενο μπροστά του;
  1. Βήμα 1 – Μετατροπή σε δευτερόλεπτα: .................................................................
  2. Βήμα 2 – Υπολογισμός μέτρων: ..................................................................
  3. Βήμα 3 – Μετατροπή σε εκατοστά: ........................................................…
  4. Βήμα 4 – Διαίρεση με το 2 : .................................................................

Μικροί χάκερ – Απόσταση, χρόνος, αισθητήρας υπέρηχων

Σελίδα 2 από 2

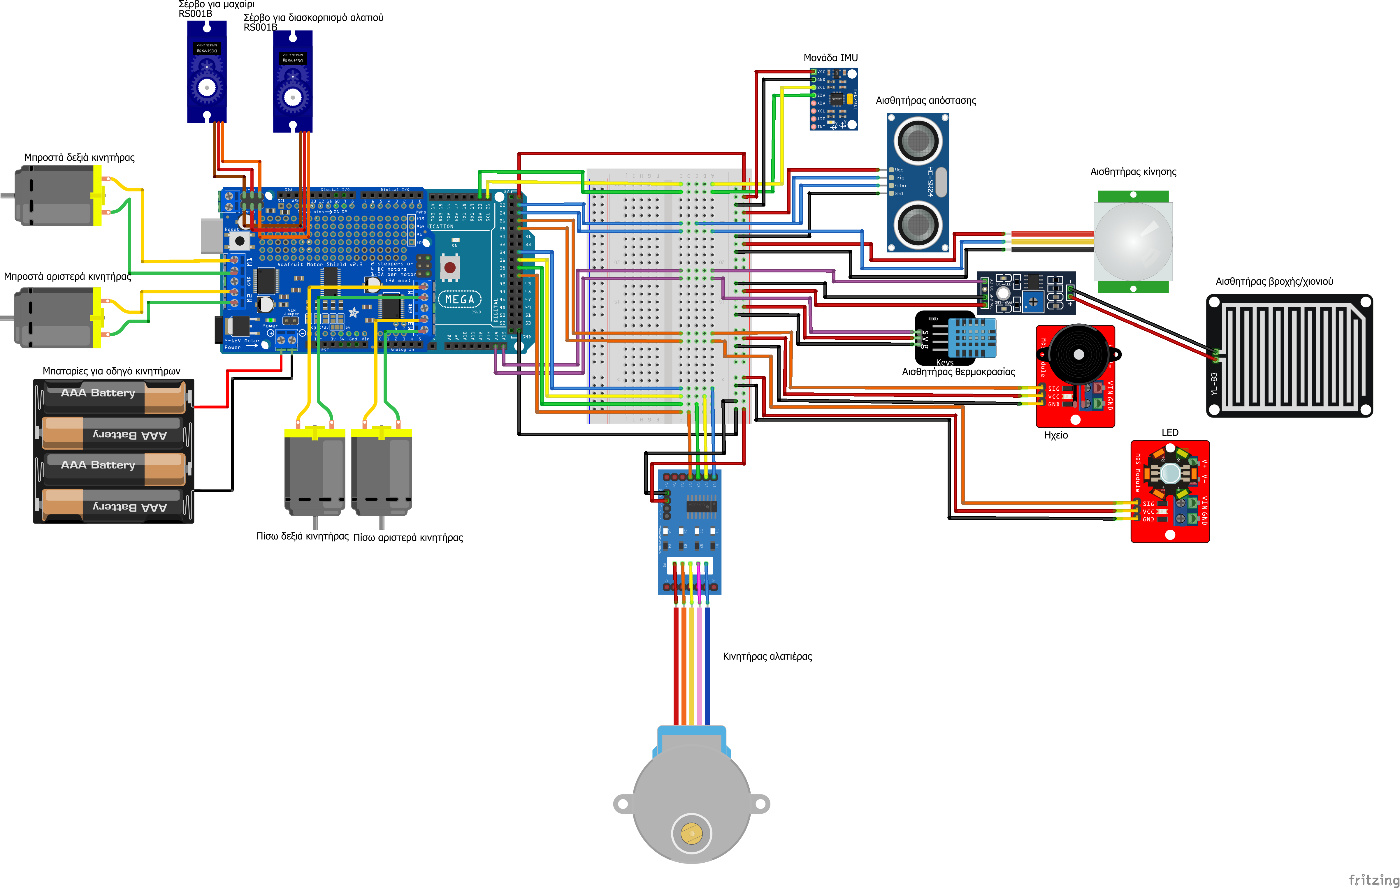
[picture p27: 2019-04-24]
Schematics/Snow plow full.png

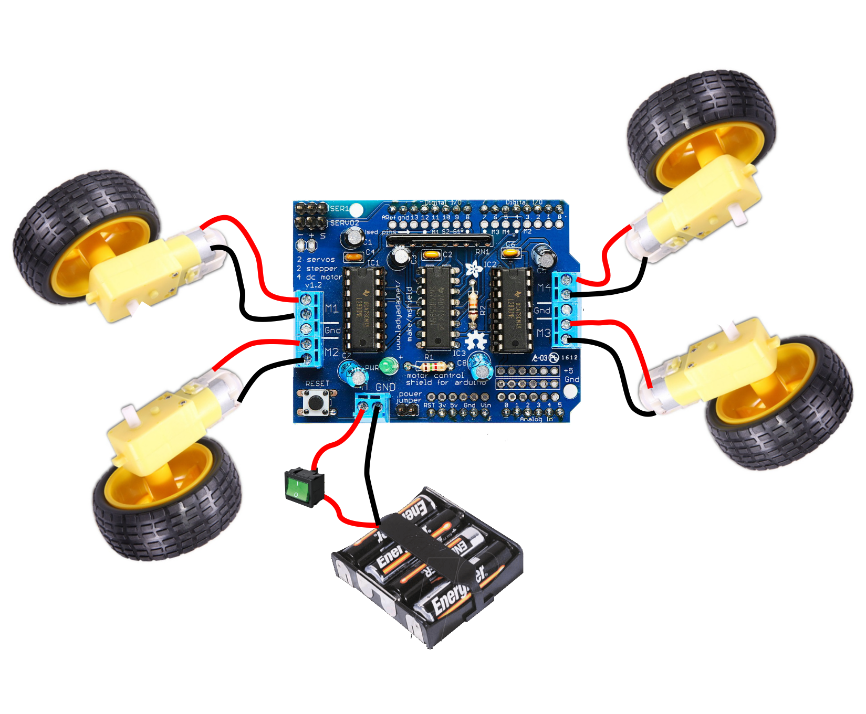
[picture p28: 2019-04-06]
Schematics/Motor Driver Shield 4 Motors 4 pins.png

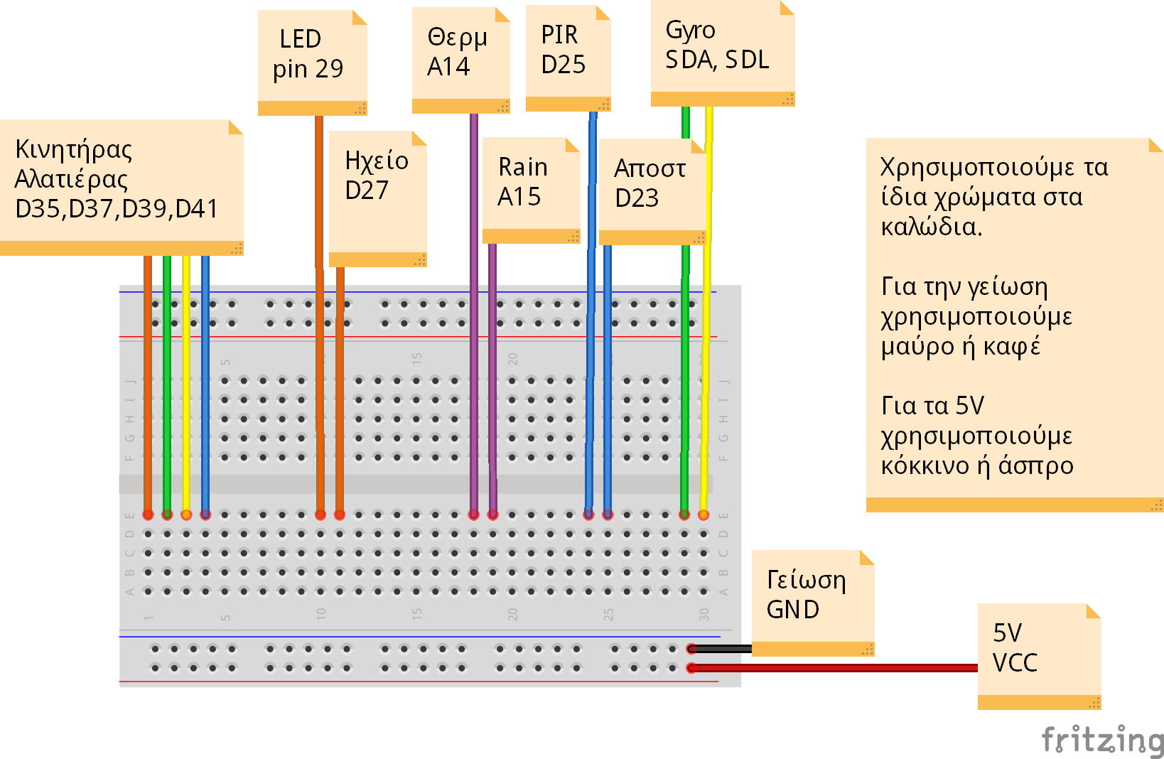
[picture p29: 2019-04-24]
Schematics/Breadboard connections_bb.png

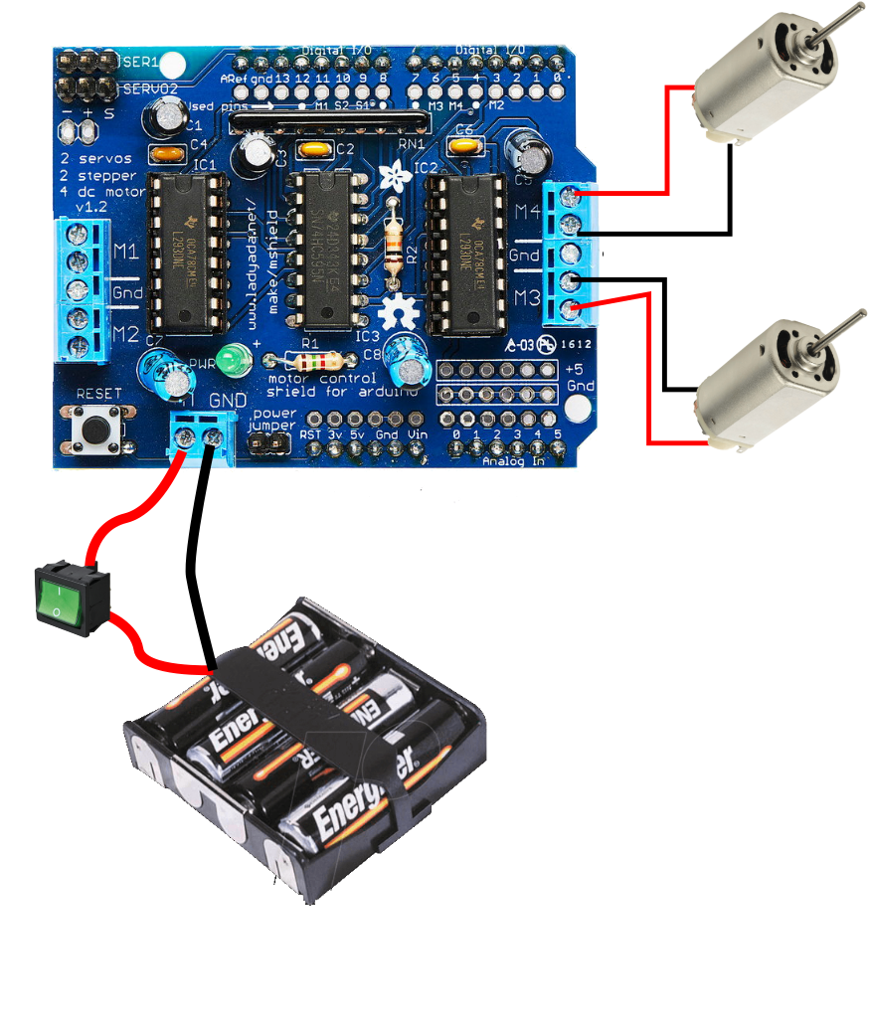
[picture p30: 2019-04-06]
Schematics/Motor Driver Shield 2 motors.png

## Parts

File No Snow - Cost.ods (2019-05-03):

No Snow – Ανάλυση κόστους υλικών για 3 αποχιονιστικά μηχανήματα
Είδος | Τιμή μονάδας | Ποσότητα | Κόστος | Link
4WD Smart Car Robot Chassis for Arduino | 18,00 € | 1 | 18,00 € | https://www.cableworks.gr/ilektronika/arduino-and-microcontrollers/kit/4wd-smart-car-robot-chassis-for-arduino/
4WD Smart Robot Car Chassis Kit for Arduino with Speed Encoder for Arduino | 19,00 € | 1 | 19,00 € | https://www.cableworks.gr/ilektronika/arduino-and-microcontrollers/kit/4wd-smart-robot-car-chassis-kit-for-arduino-with-speed-encoder-for-arduino/
3-8V DIY Shock Absorbed Smart Robot Tank Chassis With 130 Motor For Arduino | 27,00 € | 1 | 27,00 € | https://www.cableworks.gr/ilektronika/arduino-and-microcontrollers/kit/3-8v-diy-shock-absorbed-smart-robot-tank-chassis-with-130-motor-for-arduino/
Arduino Mega | 18,00 € | 3 | 54,00 € | https://www.cableworks.gr/ilektronika/arduino-and-microcontrollers/microcontrollers/compatible-boards/arduino-mega2560-r3-atmega2560-16au-board-with-atmega16u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
L293D Motor Driver Shield | 5,00 € | 3 | 15,00 € | https://www.cableworks.gr/ilektronika/arduino-and-microcontrollers/motors/drivers/l293d-motor-driver-shield-expansion-board-for-arduino/
HC-SR04 Ultrasonic Module | 2,00 € | 3 | 6,00 € | https://www.cableworks.gr/ilektronika/arduino-and-microcontrollers/sensors/sound/hc-sr04-ultrasonic-module-distance-measuring-transducer-sensor-for-arduino/
PIR HC-SR501 detector module | 2,00 € | 3 | 6,00 € | https://www.cableworks.gr/ilektronika/arduino-and-microcontrollers/sensors/distance/pir-motion-detector-module-hc-sr501-for-arduino/
MPU-6050 3 axis gyroscope and accelerometer module | 4,80 € | 3 | 14,40 € | https://www.cableworks.gr/ilektronika/arduino-and-microcontrollers/sensors/tilt/mpu-6050-3-axis-gyroscope-accelerometer-module-for-arduino-gy-521/
Raindrops Detections Sesnor module | 2,00 € | 3 | 6,00 € | https://www.cableworks.gr/ilektronika/arduino-and-microcontrollers/sensors/temperature/raindrops-detection-sensor-module-for-arduino/
DHT11 Digital Temperature and Humidity Sensor | 2,00 € | 3 | 6,00 € | https://www.cableworks.gr/ilektronika/arduino-and-microcontrollers/sensors/temperature/dht11-digital-temperature-and-humidity-sensor-for-arduino/
Sg90 TowerPro Micro Servo | 4,00 € | 6 | 24,00 € | https://www.cableworks.gr/ilektronika/arduino-and-microcontrollers/motors/servo/sg90-towerpro-micro-servo-for-rc-arduino/
28BYJ-48-5V Stepper motor + DRIVER BOARD ULN2003 | 4,00 € | 3 | 12,00 € | https://www.cableworks.gr/ilektronika/arduino-and-microcontrollers/motors/stepper/5v-28byj-48-5v-4-phase-stepper-stepper-motor-driver-board-uln2003-green-for-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
3W High Power Led Module | 2,50 € | 3 | 7,50 € | https://www.cableworks.gr/ilektronika/arduino-and-microcontrollers/outputs/keyes-3w-high-power-led-module-for-arduino/
Active Buzzer Alarm Module | 2,00 € | 3 | 6,00 € | https://www.cableworks.gr/ilektronika/arduino-and-microcontrollers/outputs/active-buzzer-alarm-module-for-arduino/
9V 6XAA BATTERY HOLDER | 1,50 € | 3 | 4,50 € | https://www.cableworks.gr/ilektronika/batteries/cases/9v-6xaa-battery-holder-for-arduino/
6V 4XAA BATTERY HOLDER | 1,50 € | 2 | 3,00 € | https://www.cableworks.gr/ilektronika/batteries/cases/6v-4xaa-battery-holder-case-for-arduino/
Powerbank 8000 mAh | 10,00 € | 1 | 10,00 € | https://www.e-jumbo.gr/achtypites-jumbotimes/power-bank-lefko-8000-mah-2-thyres-_274916/
Σύνολο |  |  | 238,40 €

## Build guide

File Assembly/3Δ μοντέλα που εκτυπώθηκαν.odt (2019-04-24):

Τρισδιάστατα μοντέλα που κατασκευάστηκαν στον 3Δ εκτυπωτή του ομίλου και αξιοποιήθηκαν στην κατασκευή των οχημάτων:

- Servo mount bracket by atoomnet - https://www.thingiverse.com/thing:1310167 Το χρησιμοποιήσαμε για να στερεώσουμε τους κινητήρες σέρβο (μαχαίρι και διασκορπιστής αλατιού) στα οχήματα μας.
- Snow Plow for a RC Car or Truck by reedwc - https://www.thingiverse.com/thing:2014767 Το χρησιμοποιήσαμε για να κατασκευάσουμε το μαχαίρι απομάκρυνσης του χιονιού.
- Snow plow Arm by ioarvanit - https://www.tinkercad.com/things/2YXBnRZX18u Τροποποίηση του βραχίονα του Snow Plow for a RC Car or Truck για καλύτερη λειτουργία.
- 5v Stepper Motor Mount and Auger by TeamKRF - https://www.thingiverse.com/thing:2797002 Αποτέλεσε το σύστημα μεταφοράς του αλατιού από την δεξαμενή στον διασκορπιστή για το όχημα 4WD, ενώ στο 2ο όχημα μας χρησιμοποιήσαμε μόνο τον ατέρμονα κοχλία, αφού είχαμε κατασκευάσει την δεξαμενή με μακετόχαρτο.

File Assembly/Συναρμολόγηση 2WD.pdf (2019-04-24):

Σέρβο για
μαχαίρι

Σέρβο για
διασκορπιστή
αλατιού

# 1ος όροφος

# 2ος όροφος

## Κινητήρες DC

Μπαταρίες για
motor shield

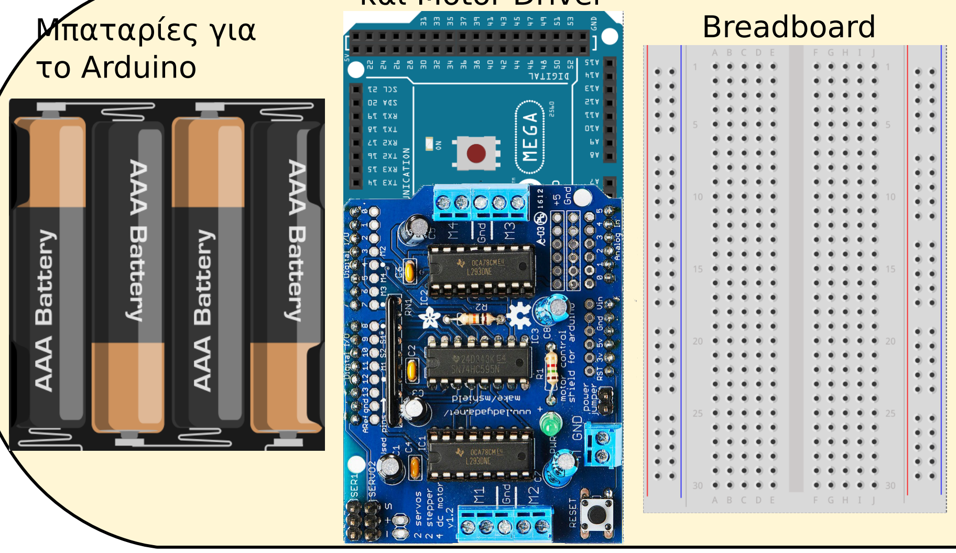
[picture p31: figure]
Μπαταρίες για το Arduino; Breadboard
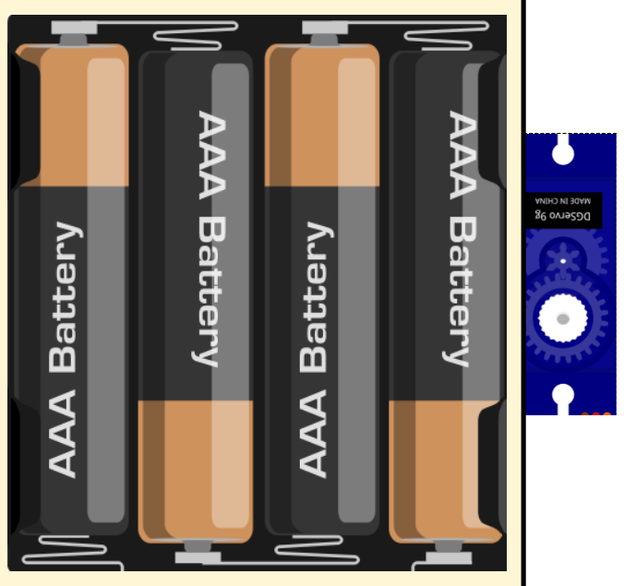
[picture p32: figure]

Arduino Mega
και Motor Driver

# Συναρμολόγηση αποχιονιστικού 2

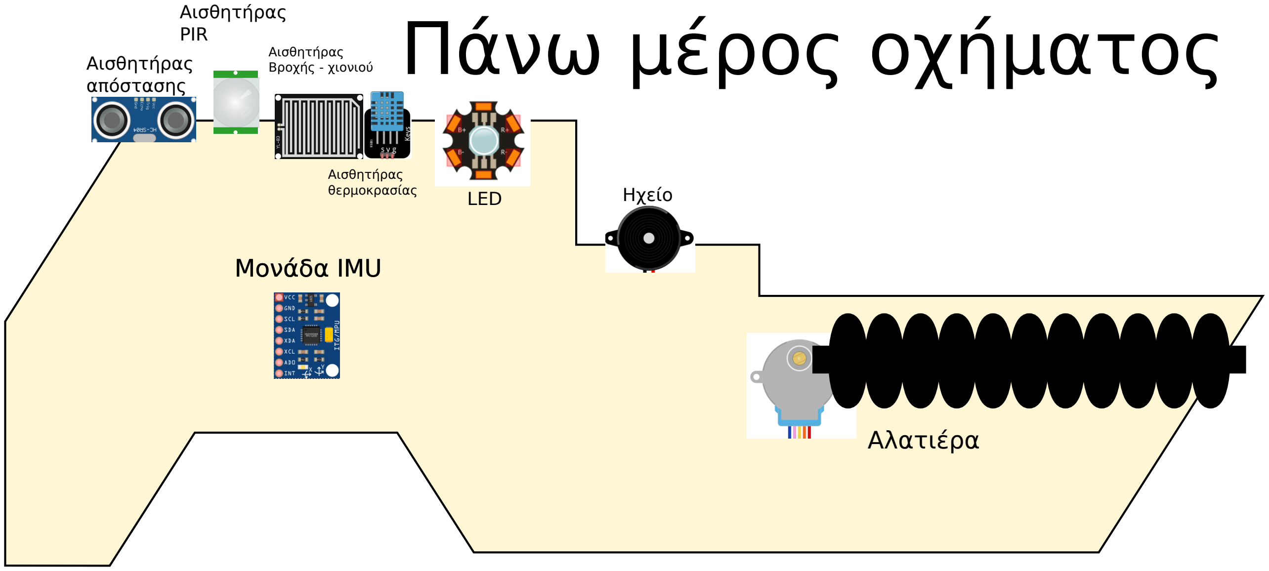
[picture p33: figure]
Μονάδα IMU; Πάνω μέρος οχήματος; Αισθητήρας απόστασης; Αισθητήρας PIR; Αισθητήρας Βροχής - χιονιού; Αισθητήρας; θερμοκρασίας; LED; Ηχείο; Αλατιέρα

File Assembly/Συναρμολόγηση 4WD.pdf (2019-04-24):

Σέρβο για
μαχαίρι

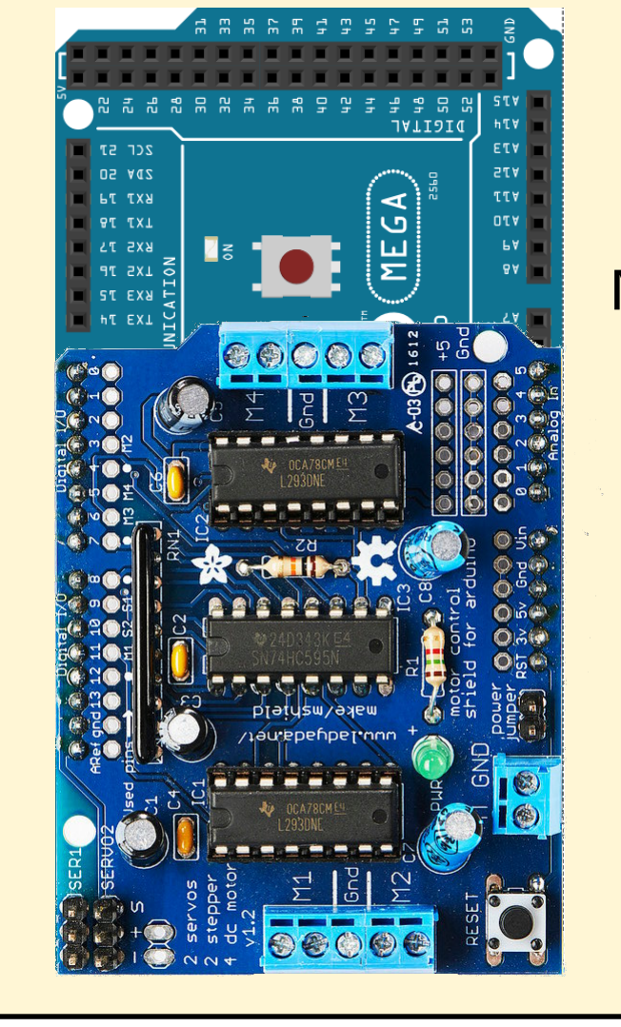
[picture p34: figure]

Arduino Mega
και Motor Driver

Μονάδα IMU

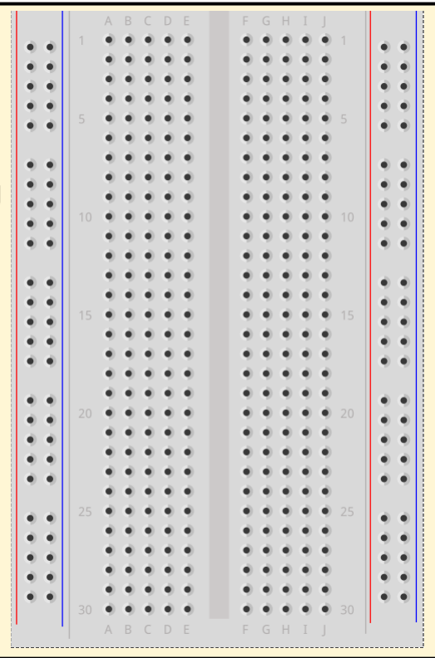
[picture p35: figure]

Breadboard

Σέρβο για
διασκορπιστή αλατιο

# 1ος όροφος

# 2ος όροφος

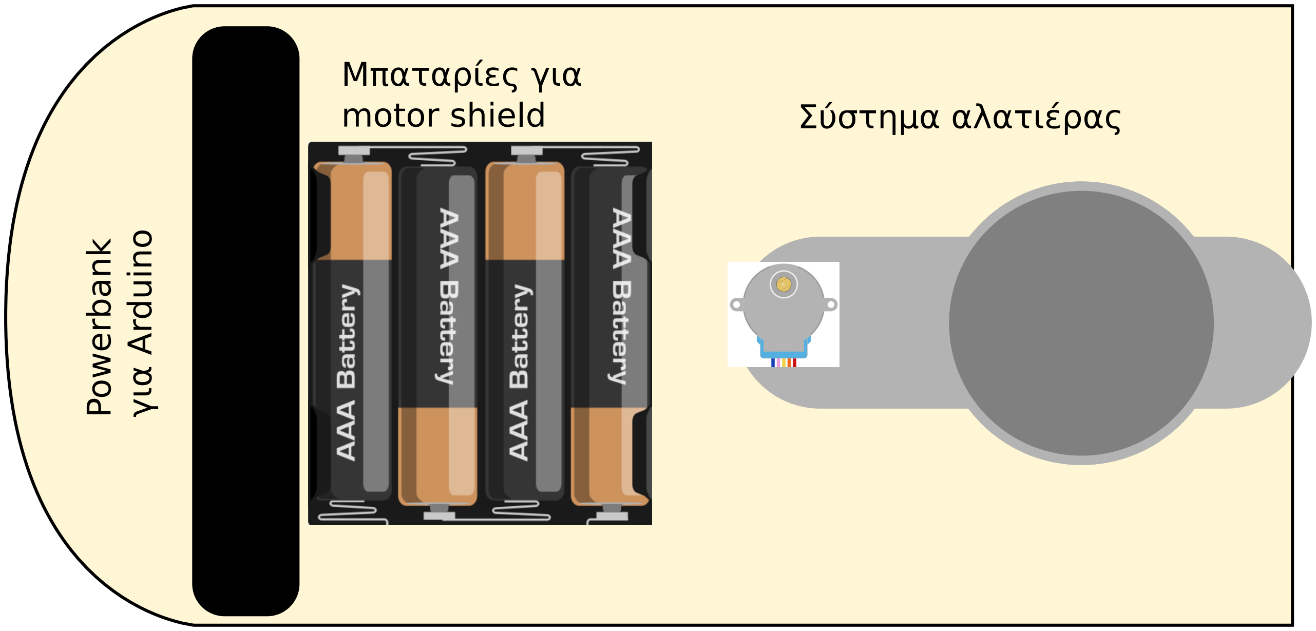
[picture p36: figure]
Powerbank; για Arduino; Μπαταρίες για; motor shield; Σύστημα αλατιέρας

# 3ος όροφος

Αισθητήρας
απόστασης

Αισθητήρας
PIR

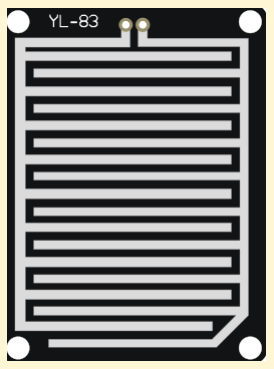
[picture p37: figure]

Αισθητήρας
Βροχής - χιονιού

Αισθητήρας
θερμοκρασίας

LED

Ηχείο

# Συναρμολόγηση αποχιονιστικού 1

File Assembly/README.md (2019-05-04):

Λίστα με τα 3Δ αντικείμενα που κατασκευάστηκαν στον 3Δ εκτυπωτή του ομίλου και σχεδιαγράμματα συναρμολόγησης και τοποθέτησης των μονάδων στα οχήματα.

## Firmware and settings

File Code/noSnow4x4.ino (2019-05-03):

/*
  Το προγραμμα για το αποχιονιστικό μηχάνημα
*/

//Εισάγουμε όλες τις βιβλιοθήκες που θα χρειαστούμε
#include <dht.h>            //Αισθητήρας θερμοκρασίας DHT11
#include <NewPing.h>        //Αισθητήρας απόστασης υπέρηχων
#include <MPU6050_tockn.h>  //Μονάδα IMU (γυροσκόπιο)
#include <Wire.h>           //Βοηθητική για την μονάδα IMU
#include <AFMotor.h>        //Οδηγός των κινητήρων για τις ρόδες
#include <Servo.h>          //Servo κινητήρες για μαχαίρι και διασκορπιστή αλατιού
#include <Stepper.h>        //Βηματικός κινητήρας για μεταφορά αλατιού

//Ορίζουμε τα pin στα οποία έχουμε συνδέσει τις μονάδες σαν σταθερές με την εντολή define
//Έτσι αντί να χρησιμοποιούμε πλέον τους αριθμούς των pin στο πρόγραμμα μας θα χρησιμοποιούμε
//τα ονόματα που δίνουμε παρακάτω
#define pinT A14      //Αισθητήρας θερμοκρασίας DHT11 είναι στο pin Α14
#define pinR A15      //Αισθητήρας βροχής είναι στο pin Α15
#define pinD 23       //Αισθητήρας απόστασης είναι στο pin 23
#define pinP 25       //Αισθητήρας PIR είναι στο pin 25
#define pinS 27       //To ηχείο είναι στο pin 27
#define pinL 29       //To φως είναι στο pin 29
#define pinServoM 10  //To Servo του μαχαιριού είναι τοποθετημένο στην θέση SERVO2 του οδηγού που αντιστοιχεί στο digital pin 10
#define pinServoA 9   //To Servo της αλατιέρας είναι τοποθετημένο στην θέση SERVO1 του οδηγού που αντιστοιχεί στο digital pin 9

#define STEPPER_PIN_1 35
#define STEPPER_PIN_2 37
#define STEPPER_PIN_3 39
#define STEPPER_PIN_4 41
int step_number = 0;

//Δημιουργούμε αντικείμενα - μεταβλητές, τα οποία έχουν τις δικές τους συναρτήσεις
Servo front;                            //Κινητήρας servo που ελέγχει το μαχαίρι
Servo back;                             //Κινητήρας servo που ελέγχει τον διασκορπιστή αλατιού
//Stepper salt(1019, 35, 37, 39, 41);     //Κινητήρας βηματικός που ελέγχει τον κοχλία μεταφοράς αλατιού. Δηλώνουμε τα βήματα (1019) και σε ποια pin είναι συνδεδεμένος
dht DHT;                                //Μονάδα αισθητήρα θερμοκρασίας
MPU6050 imu(Wire);                      //Μονάδα IMU
NewPing sonar(pinD, pinD, 400);         //Μονάδα αισθητήρα απόστασης υπέρηχων. Δηλώνουμε σε ποιο pin είναι τα TRIG και ECHO (στο ίδιο pin) καθώς και το μέγιστο όριο απόστασης 

//Δηλώνουμε τους 4 κινητήρες του οχήματος σε ποιες θέσεις είναι τοποθετημένα
AF_DCMotor motorFR(1);   //Ονομάζουμε motorFR τον κινητήρα που είναι στην θέση 1 του οδηγού κινητήρων και είναι στο μπροστά δεξί μέρος
AF_DCMotor motorFL(2);   //Ονομάζουμε motorFL τον κινητήρα που είναι στην θέση 2 του οδηγού κινητήρων και είναι στο μπροστά αριστερό μέρος
AF_DCMotor motorBL(3);   //Ονομάζουμε motorΒL τον κινητήρα που είναι στην θέση 3 του οδηγού κινητήρων και είναι στο πίσω αριστερό μέρος
AF_DCMotor motorBR(4);   //Ονομάζουμε motorBR τον κινητήρα που είναι στην θέση 4 του οδηγού κινητήρων και είναι στο πίσω δεξί μέρος

//Μεταβλητές που θα χρειαστούμε
int pir;                //Εδώ θα διαβάζουμε την τωρινή τιμή από τον αισθητήρα PIR
float cm;               //Εδώ θα διαβάζουμε την τιμή από τον αισθητήρα απόστασης σε εκατοστά
float rain;             //Εδώ θα διαβάζουμε την τιμή του αισθητήρα βροχής/χιονιού
float temp;             //Εδώ θα διαβάζουμε την τιμή του αισθητήρα θερμοκρασίας
float mZ;               //Εδώ θα κρατάμε τις μοίρες περιστροφής γύρω από τον άξονα Ζ από την μονάδα IMU
boolean ice = false;    //Μεταβλητή θα παίρνει 2 τιμές, False αν δεν έχει πάγο και true αν έχει πάγο


//Η συνάρτηση start κάνει την αρχικοποίηση του οχήματος μας
//Θα πρέπει να ενεργοποιήσουμε το γυροσκόπιο και να σηκώσουμε το μαχαίρι
void start() {
  delay(5000);                  //Περιμένουμε 5 δευτερόλεπτα για να τοποθετήσουμε το όχημα
  digitalWrite(pinL,HIGH);      //Ανάβουμε το φως
  Wire.begin();                 //Ξεκινάμε τις βιβλιοθήκες της μονάδα imu
  imu.begin();                  //Ξεκινάμε τις βιβλιοθήκες της μονάδα imu 
  imu.calcGyroOffsets(true);    //Ζητάμε από την μονάδα να κάνει την αρχική ρύθμιση (θέλει 3 δευτερόλεπτα)
  digitalWrite(pinL,LOW);       //Μόλις η ρύθμιση τελειώσει σβήνουμε το φως.
  front.attach(pinServoM);      //Ενεργοποιώ τον κινητήρα servo του μαχαιριού
  front.write(100);              //Ανεβάζω το μαχαίρι ;
}

//Η συνάρτηση checkIce θα ελέγχει τις συνθήκες θερμοκρασίας και βροόπτωσης/χιονόπτωσης και
//αν αυτές είναι τέτοιες ώστε να υπάρχει πάγος θα κάνει την μεταβλητή ice true αλλιώς θα την κάνει false
void checkIce() {
  DHT.read11(pinT);                           //Διαβάζουμε τις τιμές από τον αισθητήρα θερμοκρασίας
  temp = DHT.temperature;                     //Παίρνουμε την θερμοκρασία στην μεταβλητή temp
  rain = map(analogRead(pinR),0,1023,100,0);  //Παίρνουμε την τιμή της βροχόπτωσης/χιονόπτωσης
  if (temp > 0 && rain < 90) {                //Αν η θερμοκρασίας είναι κάτω από 0 και υπάρχει βροόπτωση/χιονόπτωση πάνω από 20% τότε
    ice = true;                              //Κάνω την μεταβλητή του πάγου σε true  
  } else {                                    //Αλλιώς
    ice = false;                             //Κάνω την μεταβλητή του πάγου σε false  
  }
}

//Η συνάρτηση checkPir ελέγχει αν υπάρχει κίνηση ανθρώπων μπροστά από το όχημα και το σταματάει εκπέμποντας προειδοποιητικό ήχο και φως
void checkPir() {
  pir = digitalRead(pinP);      //Διαβάζω την τιμή του αισθητήρα PIR
  if (pir == HIGH) {            //Αν υπάρχει κίνηση
    motorFR.run(RELEASE);       //Απενεργοποιώ τους κινητήρες
    motorBR.run(RELEASE);       //Απενεργοποιώ τους κινητήρες
    motorFL.run(RELEASE);       //Απενεργοποιώ τους κινητήρες 
    motorBL.run(RELEASE);       //Απενεργοποιώ τους κινητήρες 
    digitalWrite(pinL,HIGH);    //Ανάβω το φως 
    //digitalWrite(pinS,HIGH);    //Ανοίγω το ηχείο 
  } else {                      //Αλλιώς αν δεν υπάρχει κίνηση 
    digitalWrite(pinL,LOW);     //Κλείνω το φως 
    //digitalWrite(pinS,LOW);   //Κλείνω το ηχείο 
    motorFR.run(FORWARD);       //Ενεργοποιώ τους κινητήρες
    motorBR.run(FORWARD);       //Ενεργοποιώ τους κινητήρες
    motorFL.run(FORWARD);       //Ενεργοποιώ τους κινητήρες
    motorBL.run(FORWARD);       //Ενεργοποιώ τους κινητήρες
  }
}

//Η συνάρτηση drive οδηγεί το όχημα σε ευθεία στις μοίρες m που θέλουμε 
//Έτσι αν το όχημα μας κινείται μπροστά θα την γράψουμε ως drive(0), ενώ αν επιστρέφει 
//θα την γράψουμε ως drive(180)
void drive(float m) {       
  front.write(150);              //Κατεβάζω το μαχαίρι 
  motorFR.run(FORWARD);         //Ενεργοποιώ τους κινητήρες
  motorBR.run(FORWARD);         //Ενεργοποιώ τους κινητήρες
  motorFL.run(FORWARD);         //Ενεργοποιώ τους κινητήρες
  motorBL.run(FORWARD);         //Ενεργοποιώ τους κινητήρες
  cm = sonar.ping_cm();         //Παίρνουμε την απόσταση του τοίχου από τον αισθητήρα υπερήχων
  while (cm > 20 || cm == 0) {  //Όσο η απόσταση από τον τοίχο είναι μεγαλύτερη από 20 εκατοστά ή είναι μηδενική (μπορεί να μας δίνει τέτοια τιμή ο αισθητήρας αν δεν υπάρχει εμπόδιο κοντά
    checkPir();                 //Καλούμε τη συνάρτηση που ελέγχει για ανθρώπους
    if (ice == true) {          //Αν υπάρχει πάγος τότε
      OneStep(false);
    }
    imu.update();               //Ανανεώνουμε τις τιμές του γυροσκόπιου
    mZ = imu.getAngleZ();       //Παίρνουμε τις μοίρες περιστροφής γύρω από τον άξονα Ζ
    if (mZ < m-2) {             //Αν η γωνία περιστροφής είναι μικρότερη από -1 μοίρα το όχημα έχει φύγει λίγο δεξιά οπότε
      motorFR.setSpeed(150);    //Δίνουμε ταχύτητα 150 στους 2 κινητήρες δεξιά  
      motorBR.setSpeed(150);    //Δίνουμε ταχύτητα 150 στους 2 κινητήρες δεξιά  
      motorFL.setSpeed(0);      //Σταματάμε τους δυο κινητήρες αριστερά
      motorBL.setSpeed(0);      //Σταματάμε τους δυο κινητήρες αριστερά
    } else if (mZ > m+2) {      //Αν η γωνία περιστροφής είναι μεγαλύτερη από 1 μοίρα το όχημα έχει φύγει λίγο αριστερά οπότε
      motorFL.setSpeed(150);    //Δίνουμε ταχύτητα 150 στους 2 κινητήρες αριστερά  
      motorBL.setSpeed(150);    //Δίνουμε ταχύτητα 150 στους 2 κινητήρες αριστερά  
      motorFR.setSpeed(0);      //Σταματάμε τους δυο κινητήρες δεξιά
      motorBR.setSpeed(0);      //Σταματάμε τους δυο κινητήρες δεξιά
    } else {                    //Αλλιώς αν δεν έχουμε ξεφύγει από την ευθεία
      motorFL.setSpeed(150);    //Ορίζουμε την ταχύτητα και δεξιά και αριστερά στο 150
      motorBL.setSpeed(150);    //Ορίζουμε την ταχύτητα και δεξιά και αριστερά στο 150
      motorFR.setSpeed(150);    //Ορίζουμε την ταχύτητα και δεξιά και αριστερά στο 150
      motorBR.setSpeed(150);    //Ορίζουμε την ταχύτητα και δεξιά και αριστερά στο 150
    }
    cm = sonar.ping_cm();       //Παίρνουμε ξανά την απόσταση του τοίχου από τον αισθητήρα υπερήχων   
  }                             
  motorFR.run(RELEASE);         //Όταν πλέον φτάσουμε στον τοίχο απενεργοποιούμε τους 4 κινητήρες
  motorBR.run(RELEASE);         //Aπενεργοποιούμε τους 4 κινητήρες
  motorFL.run(RELEASE);         //Απενεργοποιούμε τους 4 κινητήρες
  motorBL.run(RELEASE);         //Απενεργοποιούμε τους 4 κινητήρες
  front.write(100);              //Ανεβάζω το μαχαίρι 
}

//Η συνάρητση turnLeft στρίβει το όχημα μας αριστερά μέχρι να φτάσει τις m μοίρες
void turnLeft(float m) {    
  while (mZ < m) {          //Όσο ακόμα δεν έχει φτάσει το όχημα τις επιθυμητές μοίρες
    motorFL.run(BACKWARD);   //Βάζω τους αριστερά κινητήρες να κινηθούν ανάποδα
    motorBL.run(BACKWARD);   //Βάζω τους αριστερά κινητήρες να κινηθούν ανάποδα
    motorFR.run(FORWARD);    //Τους δεξιά κινητήρες να κινηθούν μπροστά
    motorBR.run(FORWARD);    //Τους δεξιά κινητήρες να κινηθούν μπροστά
    motorFL.setSpeed(200);   //Ορίζω την ταχύτητα των κινητήρων
    motorBL.setSpeed(200);   //Ορίζω την ταχύτητα των κινητήρων
    motorFR.setSpeed(200);   //Ορίζω την ταχύτητα των κινητήρων
    motorBR.setSpeed(200);   //Ορίζω την ταχύτητα των κινητήρων
    imu.update();           //Ενημερώνω τις τιμές του γυροσκόπιου
    mZ = imu.getAngleZ();   //Παίρνω τη νέα τιμής της γωνίας Z
  }
  motorFR.run(RELEASE);      //Όταν πλέον φτάσω τις επιθυμητές μοίρες απενεργοποιώ τους κινητήρες
  motorBR.run(RELEASE);      //Απενεργοποιώ τους κινητήρες
  motorFL.run(RELEASE);      //Απενεργοποιώ τους κινητήρες
  motorBL.run(RELEASE);      //Απενεργοποιώ τους κινητήρες
}

//Η συνάρητση turnRight στρίβει το όχημα μας αριστερά μέχρι να φτάσει τις m μοίρες
void turnRight(float m) {    
  while (mZ > m) {          //Όσο ακόμα δεν έχει φτάσει το όχημα τις επιθυμητές μοίρες
    motorFR.run(BACKWARD);   //Βάζω τους δεξιά κινητήρες να κινηθούν ανάποδα
    motorBR.run(BACKWARD);   //Βάζω τους δεξιά κινητήρες να κινηθούν ανάποδα
    motorFL.run(FORWARD);    //Τους αριστερά κινητήρες να κινηθούν μπροστά
    motorBL.run(FORWARD);    //Τους αριστερά κινητήρες να κινηθούν μπροστά
    motorFL.setSpeed(200);   //Ορίζω την ταχύτητα των κινητήρων
    motorBL.setSpeed(200);   //Ορίζω την ταχύτητα των κινητήρων
    motorFR.setSpeed(200);   //Ορίζω την ταχύτητα των κινητήρων
    motorBR.setSpeed(200);   //Ορίζω την ταχύτητα των κινητήρων
    imu.update();           //Ενημερώνω τις τιμές του γυροσκόπιου
    mZ = imu.getAngleZ();   //Παίρνω τη νέα τιμής της γωνίας Z
  }
  motorFR.run(RELEASE);      //Όταν πλέον φτάσω τις επιθυμητές μοίρες απενεργοποιώ τους κινητήρες
  motorBR.run(RELEASE);      //Απενεργοποιώ τους κινητήρες
  motorFL.run(RELEASE);      //Απενεργοποιώ τους κινητήρες
  motorBL.run(RELEASE);      //Απενεργοποιώ τους κινητήρες
}

void setup() {
  //Ορίζω τα pin που χρειάζονται να δηλωθούν ως input και output
  pinMode(pinS,OUTPUT);   //Ορίζουμε το pin του ηχείου ως έξοδο
  pinMode(pinL,OUTPUT);   //Ορίζουμε το pin του φωτός ως έξοδο
  pinMode(pinP, INPUT);   //Ορίζουμε το pin του αισθητήρα PIR ως είσοδο
  pinMode(STEPPER_PIN_1, OUTPUT);
  pinMode(STEPPER_PIN_2, OUTPUT);
  pinMode(STEPPER_PIN_3, OUTPUT);
  pinMode(STEPPER_PIN_4, OUTPUT);
  
  //Τώρα ξεκινάν οι οδηγίες μας
  start();        //Βήμα 1ο Αρχικοποιώ το όχημα
  checkIce();     //Βήμα 2ο Ελέγχω τις συνθήκες θερμοκρασίας - υγρασίας για το αν υπάρχει πάγος
  drive(0);
  
}


void OneStep(bool dir){
    if(dir){
switch(step_number){
  case 0:
  digitalWrite(STEPPER_PIN_1, HIGH);
  digitalWrite(STEPPER_PIN_2, LOW);
  digitalWrite(STEPPER_PIN_3, LOW);
  digitalWrite(STEPPER_PIN_4, LOW);
  break;
  case 1:
  digitalWrite(STEPPER_PIN_1, LOW);
  digitalWrite(STEPPER_PIN_2, HIGH);
  digitalWrite(STEPPER_PIN_3, LOW);
  digitalWrite(STEPPER_PIN_4, LOW);
  break;
  case 2:
  digitalWrite(STEPPER_PIN_1, LOW);
  digitalWrite(STEPPER_PIN_2, LOW);
  digitalWrite(STEPPER_PIN_3, HIGH);
  digitalWrite(STEPPER_PIN_4, LOW);
  break;
  case 3:
  digitalWrite(STEPPER_PIN_1, LOW);
  digitalWrite(STEPPER_PIN_2, LOW);
  digitalWrite(STEPPER_PIN_3, LOW);
  digitalWrite(STEPPER_PIN_4, HIGH);
  break;
} 
  }else{
    switch(step_number){
  case 0:
  digitalWrite(STEPPER_PIN_1, LOW);
  digitalWrite(STEPPER_PIN_2, LOW);
  digitalWrite(STEPPER_PIN_3, LOW);
  digitalWrite(STEPPER_PIN_4, HIGH);
  break;
  case 1:
  digitalWrite(STEPPER_PIN_1, LOW);
  digitalWrite(STEPPER_PIN_2, LOW);
  digitalWrite(STEPPER_PIN_3, HIGH);
  digitalWrite(STEPPER_PIN_4, LOW);
  break;
  case 2:
  digitalWrite(STEPPER_PIN_1, LOW);
  digitalWrite(STEPPER_PIN_2, HIGH);
  digitalWrite(STEPPER_PIN_3, LOW);
  digitalWrite(STEPPER_PIN_4, LOW);
  break;
  case 3:
  digitalWrite(STEPPER_PIN_1, HIGH);
  digitalWrite(STEPPER_PIN_2, LOW);
  digitalWrite(STEPPER_PIN_3, LOW);
  digitalWrite(STEPPER_PIN_4, LOW);
 
  
} 
  }
step_number++;
  if(step_number > 3){
    step_number = 0;
  }
}


void loop() {
}

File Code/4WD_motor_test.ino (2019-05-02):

/* Πρόγραμμα για τον έλεγχο λειτουργίας των κινητήρων στο αποχιονιστικό 1
 * Το πρόγραμμα λειτουργεί όλους τους κινητήρες μπροστά για 3 δευτερόλεπτα και 
 * μετά τους απενεργοποιεί για άλλα 3 δευτερόλεπτα. Η διαδικασία αυτή επαναλαμβάνεται
 * διαρκώς. Αν κάποιος κινητήρας κινείται ανάποδα μπορούμε να αντιστρέψουμε τα καλώδια του
 * στο Motor Driver Shield
 */ 
 
#include <AFMotor.h>    //Προσθέτουμε την βιβλιοθήκη για τον οδηγό των κινητήρων

AF_DCMotor motorFR(1);   //Ονομάζουμε motorFR τον κινητήρα που είναι στην θέση 1 του οδηγού κινητήρων και είναι στο μπροστά δεξί μέρος
AF_DCMotor motorFL(2);   //Ονομάζουμε motorFL τον κινητήρα που είναι στην θέση 2 του οδηγού κινητήρων και είναι στο μπροστά αριστερό μέρος
AF_DCMotor motorBL(3);   //Ονομάζουμε motorΒL τον κινητήρα που είναι στην θέση 3 του οδηγού κινητήρων και είναι στο πίσω αριστερό μέρος
AF_DCMotor motorBR(4);   //Ονομάζουμε motorBR τον κινητήρα που είναι στην θέση 4 του οδηγού κινητήρων και είναι στο πίσω δεξί μέρος


void setup() {
}

void loop() {
  motorFR.run(FORWARD);    //Ενεργοποιούμε τους δεξιά κινητήρες να κινηθούν μπροστά
  motorBR.run(FORWARD);    //Ενεργοποιούμε τους δεξιά κινητήρες να κινηθούν μπροστά
  motorFR.setSpeed(200);   //Ορίζουμε την ταχύτητα των δεξιά κινητήρων μεταξύ του 0-255
  motorBR.setSpeed(200);   //Ορίζουμε την ταχύτητα των δεξιά κινητήρων μεταξύ του 0-255
  motorFL.run(FORWARD);    //Ενεργοποιούμε τους αριστερά κινητήρες να κινηθούν μπροστά
  motorBL.run(FORWARD);    //Ενεργοποιούμε τους αριστερά κινητήρες να κινηθούν μπροστά
  motorFL.setSpeed(200);   //Ορίζουμε την ταχύτητα των αριστερά κινητήρων μεταξύ του 0-255
  motorBL.setSpeed(200);   //Ορίζουμε την ταχύτητα των αριστερά κινητήρων μεταξύ του 0-255
  delay(3000);             //Περιμένουμε 3 δευτερόλεπτα
   
  motorFR.run(RELEASE);    //Απενεργοποιούμε τους δεξιά κινητήρες
  motorBR.run(RELEASE);    //Απενεργοποιούμε τους δεξιά κινητήρες
  motorFL.run(RELEASE);    //Απενεργοποιούμε τους αριστερά κινητήρες
  motorBL.run(RELEASE);    //Απενεργοποιούμε τους αριστερά κινητήρες
  delay(3000);             //Περιμένουμε 3 δευτερόλεπτα
}
